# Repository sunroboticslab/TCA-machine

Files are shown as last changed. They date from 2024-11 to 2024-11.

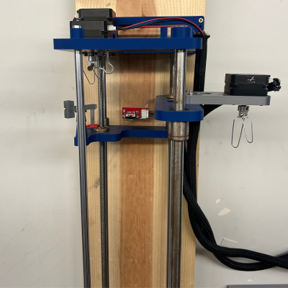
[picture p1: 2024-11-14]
TCA_Machine_Version_2/04 Photos/Picture2.png

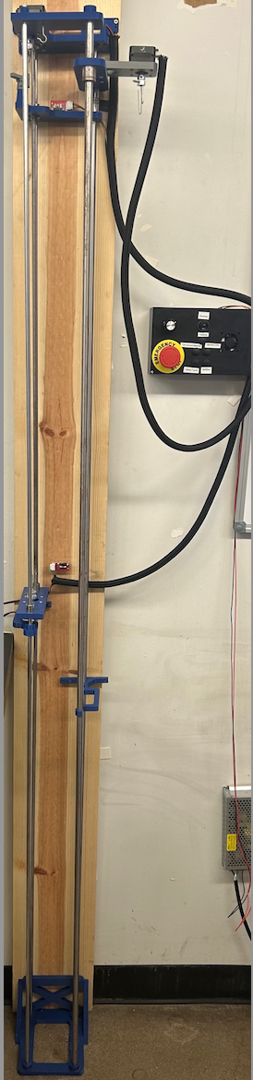
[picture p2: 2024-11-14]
TCA_Machine_Version_2/04 Photos/Picture1.png

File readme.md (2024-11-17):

<h1 align="center">Twisted and Coiled Actuator (TCA) Machine - V1 & V2</h1>

<p>Welcome to the Twisted and Coiled Actuator (TCA) Machine project repository! This project involves the design, manufacturing, and development of two versions of a machine used to fabricate TCAs for soft robotic applications. TCAs mimic biological actuators and are ideal for creating compliant, adaptive, and resilient robots. This repository contains the models, control software, documentation, and more for both versions of the TCA machine.</p>

<h2>Project Overview</h2>

<p>The TCA Machine is an automated fabrication system designed to create free stroke twisted and coiled actuators for use in soft robotic systems. These actuators provide high contraction ratios and are useful for many robotic applications, such as actuating tensegrity robots and shape-morphing quadrupedal robots.</p>

<p>There are two versions of the TCA machine available in this repository:</p>

<ul>
  <li><strong>Version 1</strong></li>
  <li><strong>Version 2</strong></li>
</ul>
<h3>Differences Between Version 1 and Version 2</h3>
<ul>
  <li>Version 2 has an increased width to improve reliability and provide more room for manipulation.</li>
  <li>The pulley in Version 2 is separated from the machine and suspended in the air to reduce friction and tension in the thread.</li>
  <li>A Stepper motor was removed in Version 2 as it was redundant.</li>
  <li>Transition from latch buttons to momentary buttons for improved control.</li>
  <li>Physical limit switches were added in Version 2 for enhanced safety and control.</li>
</ul>

<h2>Repository Structure</h2>

<h3>Version 1: TCA_Machine_Version_1/</h3>
<ul>
  <li><strong>01 SolidWorks</strong>
    <ul>
      <li><strong>01 Machine:</strong> Contains SolidWorks files for the mechanical design of the TCA machine.</li>
      <li><strong>02 Control_Box:</strong> SolidWorks files for the control box design, including details of the electronics.</li>
    </ul>
  </li>
  <li><strong>02 Arduino</strong>: Arduino code to control the motors and sensors of the machine, ensuring precise coiling and twisting.</li>
  <li><strong>03 Documentation</strong>: Contains documentation related to Version 1, which are listed below.
  <ul>
      <li><strong>Parts list TCA machine.xlsx:</strong> An Excel file listing all the parts used in Version 1 of the TCA machine.</li>
      <li><strong>TCA Machine.docx:</strong> Documentation describing the purpose and operation of the TCA machine.</li>
      <li><strong>TCA Manufacturing.pptx:</strong> A PowerPoint presentation that provides insights into the manufacturing process of TCAs.</li>
      <li><strong>motor layout.pptx:</strong> A presentation detailing the layout of the motors used in Version 1.</li>
    </ul>
  </li>
  <li><strong>04 Photos</strong>: A collection of photos showcasing the machine and its components.</li>
</ul>

<h3>Version 2: TCA_Machine_Version_2/</h3>
<ul>
  <li><strong>01 SolidWorks</strong>
    <ul>
      <li><strong>01 Machine</strong>: Updated SolidWorks files for the enhanced mechanical design.</li>
      <li><strong>02 Control_Box</strong>: Updated SolidWorks files for the improved control box design.</li>
    </ul>
  </li>
<li><strong>02 Arduino/TCACodeV2.0</strong>: Improved Arduino code for Version 2, featuring optimizations for smoother operation and enhanced control.</li>
<li><strong>03 Documentation</strong>: Updated user manuals and documentation for assembling and operating Version 2.
    <ul>
    <li><strong>Instructions_manualV2.pdf</strong>: A comprehensive user manual for Version 2, detailing Mechanical Construction, Electrical Construction, and how to use the machine.</li>
    <li><strong>Motor_Layout.pdf</strong>: A PDF document detailing the motor layout in Version 2.</li>
    <li><strong>TCA_Machine_Mech_BOM.xlsx</strong>: Bill of Materials for the mechanical components in Version 2.</li>
    <li><strong>TCA_Machine_Electric_BOM.xlsx</strong>: Bill of Materials for the electrical components in Version 2.</li>
    </ul>
  </li>
  <li><strong>04 Photos</strong>: Photos of Version 2 showcasing the new features and improvements.</li>
</ul>

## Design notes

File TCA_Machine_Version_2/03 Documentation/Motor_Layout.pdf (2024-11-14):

# Motor Layout and Electrical Schematics

# Motor Layout

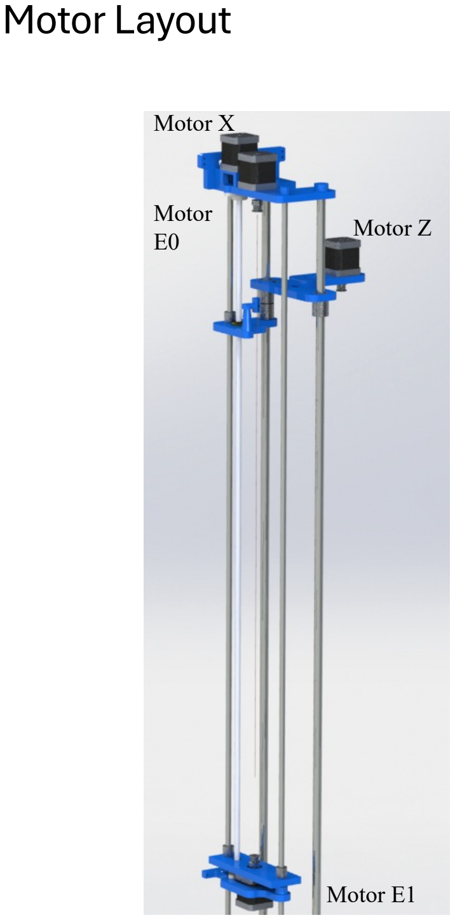
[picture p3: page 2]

Motor X

Motor
E0 | Motor Z

Motor E1

# Electrical Schematics

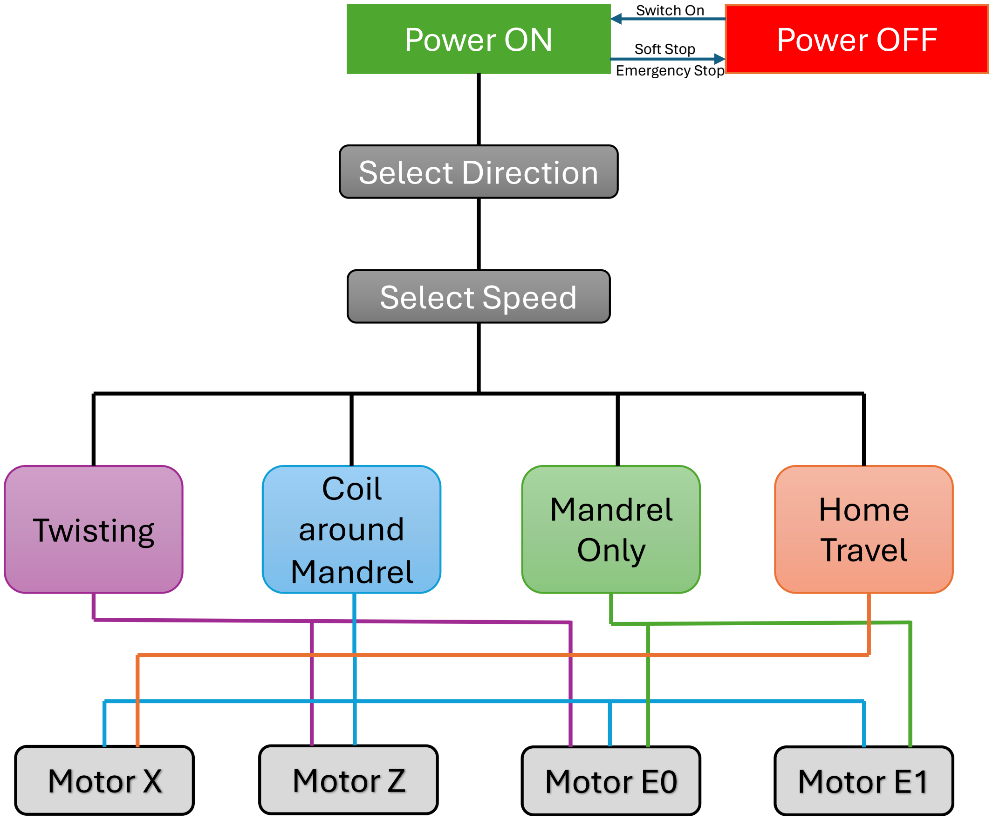
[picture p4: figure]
Power ON; Power OFF; Select Direction; Twisting; Coil around Mandrel; Mandrel Only; Home Travel; Select Speed; Motor X; Motor Z; Motor E0; Motor E1; Soft Stop; Switch On; Emergency Stop

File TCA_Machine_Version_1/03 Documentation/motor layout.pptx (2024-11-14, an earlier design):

## Motor electrical Schematics

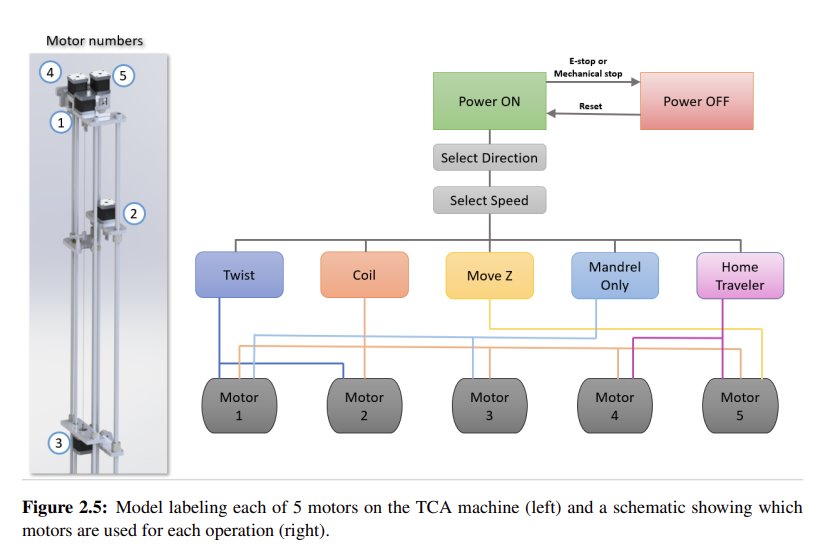
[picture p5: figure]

## Motor Orientation

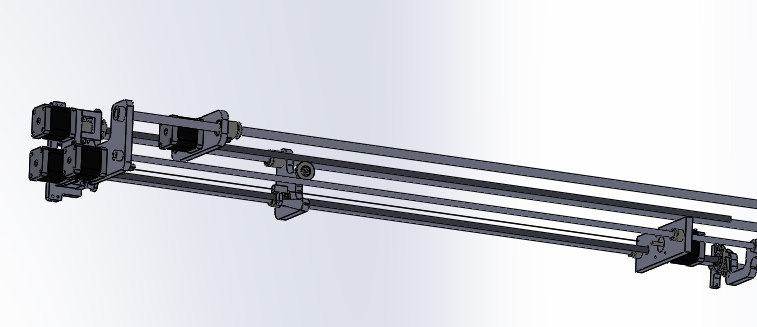
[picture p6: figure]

Y

X

Z

E0

E1

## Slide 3

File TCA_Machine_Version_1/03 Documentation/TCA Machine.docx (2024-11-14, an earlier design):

The customized machine for fabrication of the Twisted-and-Coiled Actuators.

The machine’s high is 1.8 m and we can install a precursor fiber around 3.2 m by folding the fiber around a roller at the bottom of the machine. That will allow the machine to fabricate a TCA with maximum length of 1 m within 8 min for a proficient user. The machine can be used to fabricate either extension TCA or contraction TCAs.

A control panel is installed and there are functioning buttons that can control fabrication speed, reset the machine, control individual motors and motor directions. The machine has 5 step motor that control the twisting and coiling process. Motor A and B insert twisting into a precursor fiber from the two ends of the fiber. Motor C and D rotate the mandrel and motor E control the traveling to coil the twisted fiber on a mandrel.

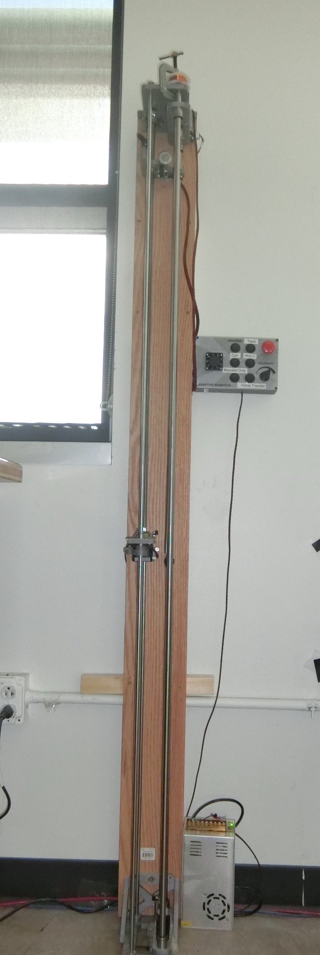
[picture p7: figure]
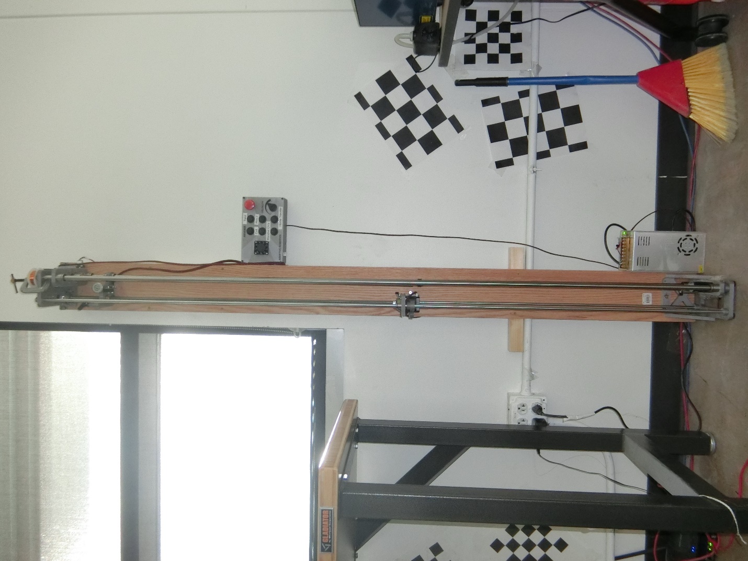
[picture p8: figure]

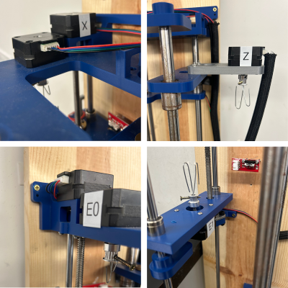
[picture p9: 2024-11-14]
TCA_Machine_Version_2/04 Photos/Picture4.png

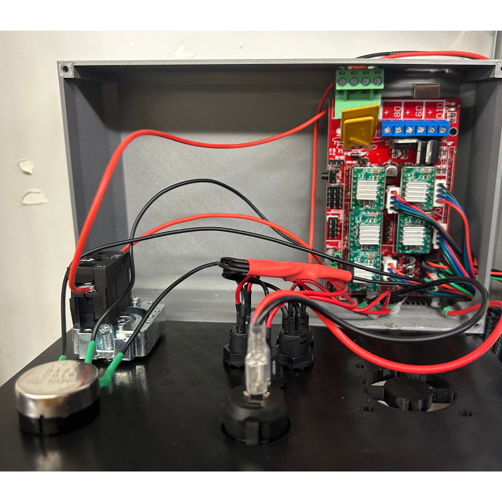
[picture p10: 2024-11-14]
TCA_Machine_Version_2/04 Photos/Picture3.png

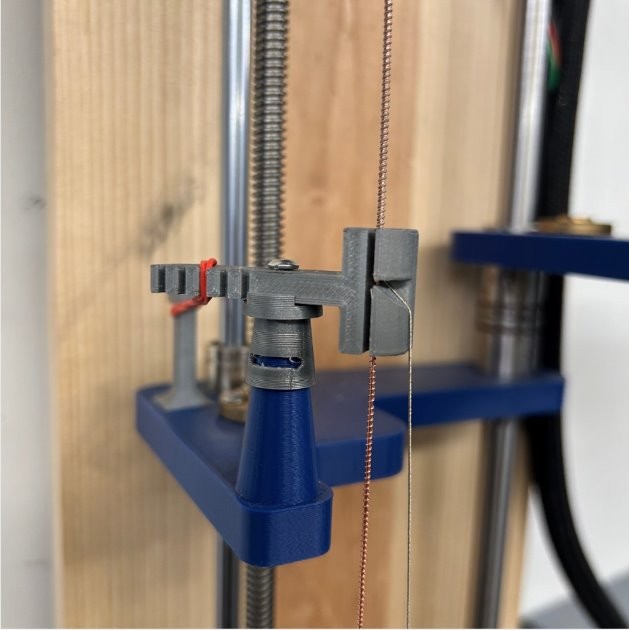
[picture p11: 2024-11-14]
TCA_Machine_Version_2/04 Photos/Picture5.jpg

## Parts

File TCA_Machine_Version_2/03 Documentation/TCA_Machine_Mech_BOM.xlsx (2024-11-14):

Name | Quantity | Unit Price | Total Price | Link
Mechanical Parts
2 meters guide rod (12mm dia) | 2 | 78.42 | 156.84 | https://www.mcmaster.com/6112K55/
1 meter guide rod (8mm) | 4 | 33.99 | 135.96 | https://a.co/d/fRVqcEy
T8 Lead Screw Set (Pitch 2mm, Lead 2mm, Length 1000mm) | 1 | 29.75 | 29.75 | https://a.co/d/94WhODm
12mm LM12UU Linear Motion Ball Bearing (10 set) | 1 | 17.21 | 17.21 | https://a.co/d/ehVNYda
8mm LM8UU Linear Motion Ball Bearing(10 Set) | 1 | 9.99 | 9.99 | https://a.co/d/6VYYZox
KFL08 Pillow Block Bearing 8mm/0.31"(4 Set) | 1 | 8.99 | 8.99 | https://a.co/d/cz1D3lo
Wood (1 in. x 12 in. x 12 ft.) | 1 | 37.98 | 37.98 | https://www.homedepot.com/p/1-in-x-12-in-x-12-ft-Premium-Kiln-Dried-Square-Edge-Whitewood-Common-Softwood-Boards-458554/100088520
Screw Hooks (.080 x 1-5/16') | 1 | 2.59 | 2.59 | https://a.co/d/eZcLpH0
M3 Button Head Screws | 1 | 16.99 | 16.99 | https://a.co/d/c4Ccx2F
M5 Button Head Screws | 1 | 7.29 | 7.29 | https://a.co/d/cdViFu4
GT2 Timing Belt Pulleys (5 Set) | 1 | 7.99 | 7.99 | https://a.co/d/6UJ3atT
Total |  |  | 431.58

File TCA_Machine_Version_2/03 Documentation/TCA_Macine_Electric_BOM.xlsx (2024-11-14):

Name | Quantity | Unit Price | Total Price | Link
Electrical Parts
NEMA 17 motors (5 Set) | 1 | 38.99 | 38.99 | https://a.co/d/bTNgY0k
NEMA 17 motor control kit (RAMPS 1.4 Controller + Arduino Mega 2560 + A4988 Motor Drivers) | 1 | 31.23 | 31.23 | https://a.co/d/d4WsQai
Mechanical EndStop Limit Switches | 1 | 8.99 | 8.99 | https://a.co/d/cJqhPcu
12mm Mini Momentary Push Button Switches(12 Set) | 1 | 9.96 | 9.96 | https://a.co/d/cWaeGQx
Emergency Stop Push Button Switch | 1 | 9.99 | 9.99 | https://a.co/d/iSiMs7G
Potentiometer | 1 | 9.55 | 9.55 | https://a.co/d/dMHleoA
12V 10A DC Universal Regulated Switching Power Supply | 1 | 24.41 | 24.41 | https://a.co/d/bmSqOKI
26 Gauge Bare Copper Wire | 1 | 7.99 | 7.99 | https://a.co/d/bAmWfGY
30 Gauge Bare Copper Wire | 1 | 9.99 | 9.99 | https://a.co/d/aIDjfT3
22 Gauge Silicone Wires | 1 | 12.48 | 12.48 | https://a.co/d/0CMNqas
12V Round Rocker Switch | 1 | 4.99 | 4.99 | https://a.co/d/810Gv5C
Power Chord | 1 | 9.99 | 9.99 | https://a.co/d/27jVXjj
Total |  |  | 178.56

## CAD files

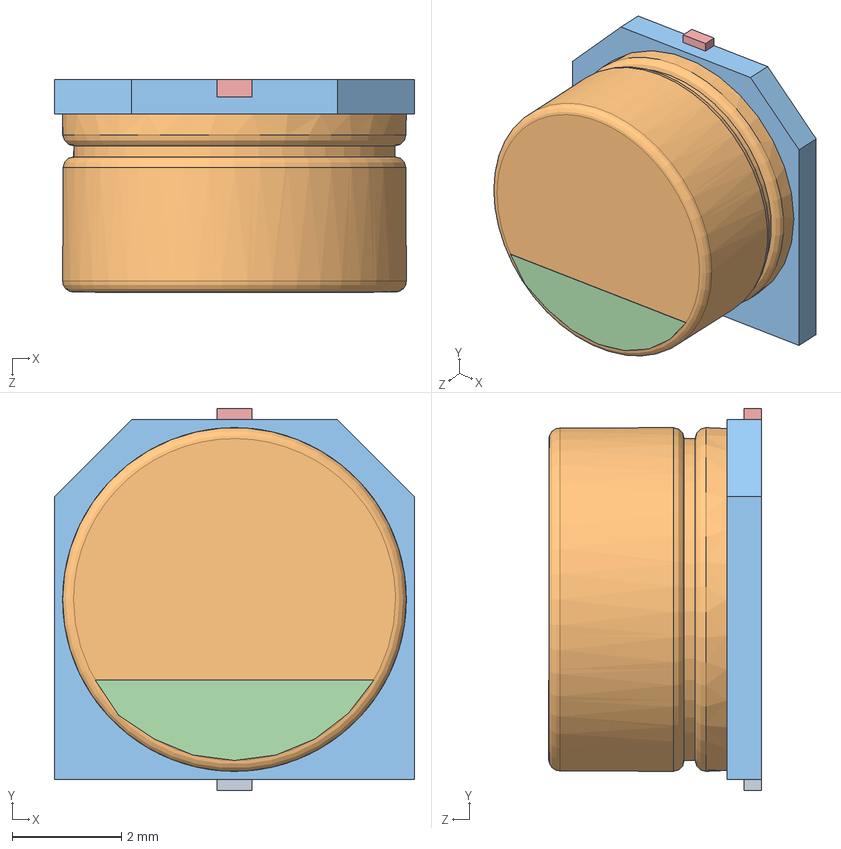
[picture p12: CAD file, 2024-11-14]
TCA_Machine_Version_2/01 SolidWorks/02 Control_Box/V2_User Library-CAPSMD6_3x3_9.SLDASM
6.60 x 7.00 x 3.91 mm
User Library-CAPSMD6_3x3_9_CAP003
User Library-CAPSMD6_3x3_9_CAP
User Library-CAPSMD6_3x3_9_CAP001
User Library-CAPSMD6_3x3_9_CAP002
User Library-CAPSMD6_3x3_9_CAP004

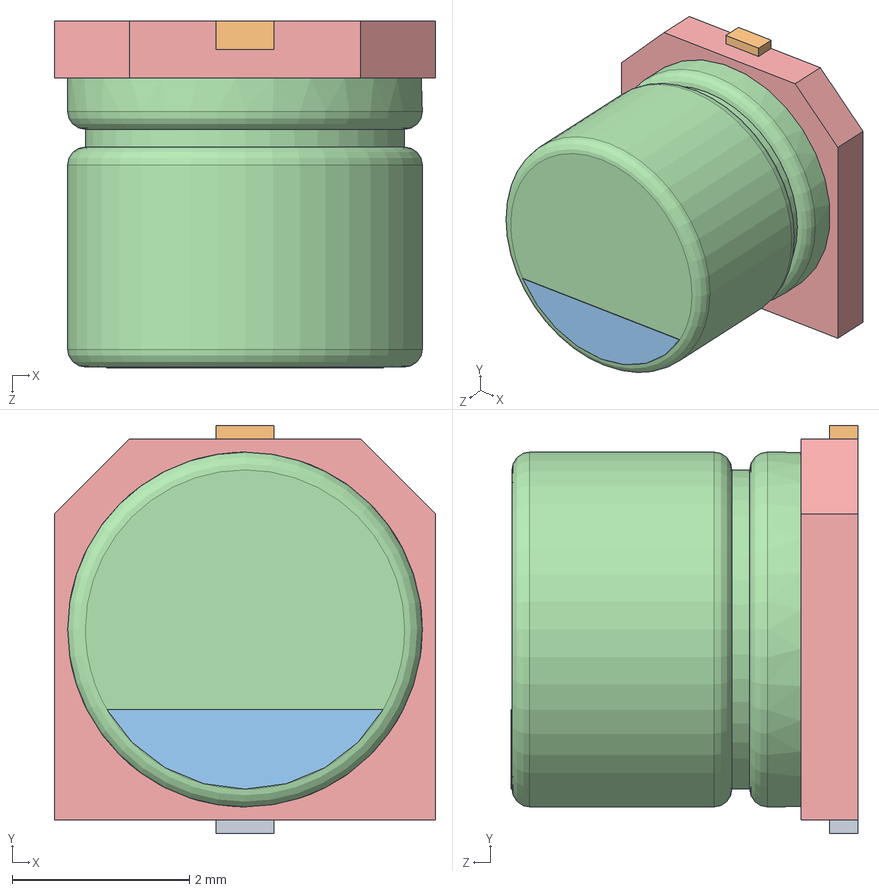
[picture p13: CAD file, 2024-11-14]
TCA_Machine_Version_2/01 SolidWorks/02 Control_Box/V2_User Library-CAPSMD4x3_9.SLDASM
4.30 x 4.60 x 3.91 mm
User Library-CAPSMD4x3_9_CAPSMD4x3_9003
User Library-CAPSMD4x3_9_CAPSMD4x3_9004
User Library-CAPSMD4x3_9_CAPSMD4x3_9002
User Library-CAPSMD4x3_9_CAPSMD4x3_9001
User Library-CAPSMD4x3_9_CAPSMD4x3_9

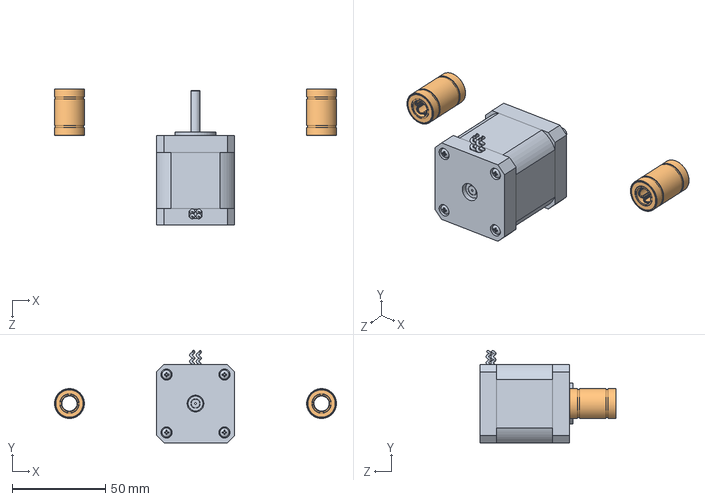
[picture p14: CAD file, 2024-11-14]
TCA_Machine_Version_2/01 SolidWorks/01 Machine/V2_TSA machine motor on sliderV2.SLDASM
151.0 x 49.5 x 73.0 mm
V2_8mm LINEAR BALL BEARNGV2 x 2
V2_Stepper Motor NEMA 17 42x42x50V2

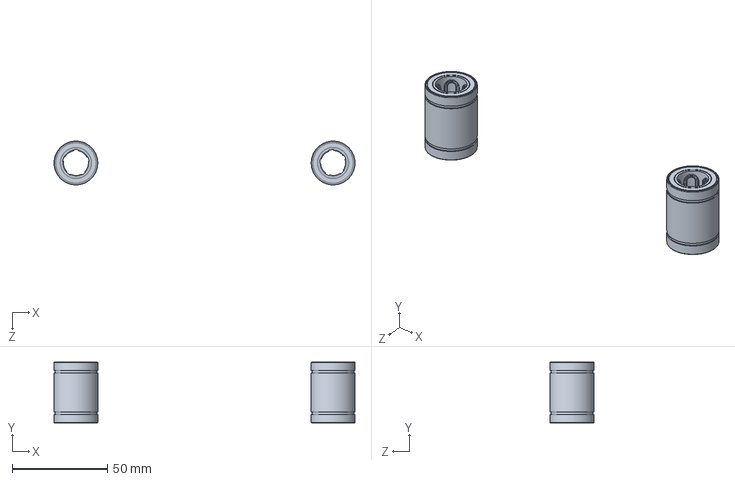
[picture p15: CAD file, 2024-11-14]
TCA_Machine_Version_2/01 SolidWorks/01 Machine/V2_TSA machine motor on slider 13mmV2.SLDASM
158.0 x 32.0 x 23.0 mm
V2_13mm LINEAR BALL BEARNGV2 x 2

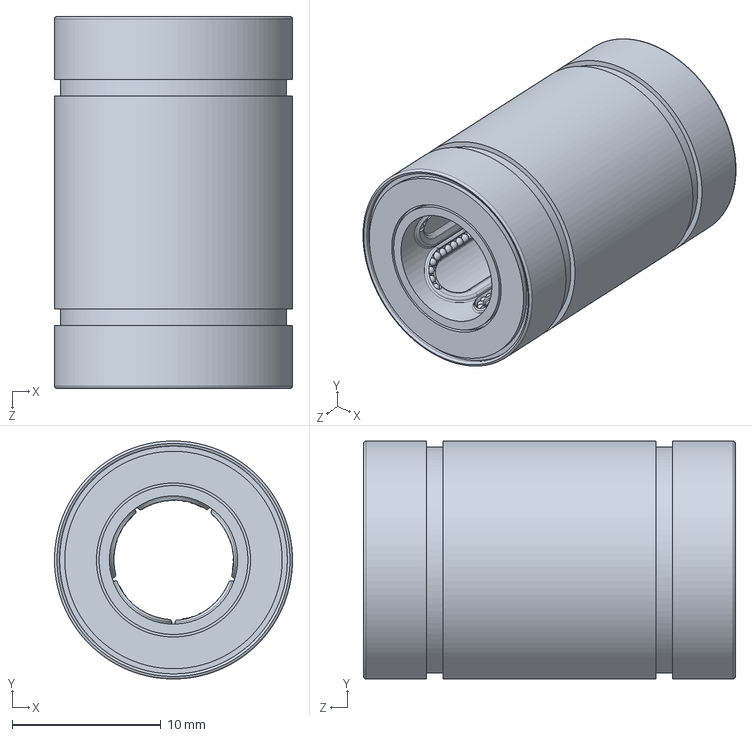
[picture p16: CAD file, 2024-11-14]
TCA_Machine_Version_2/01 SolidWorks/01 Machine/V2_8mm LINEAR BALL BEARNGV2.SLDPRT
16.0 x 16.0 x 25.0 mm

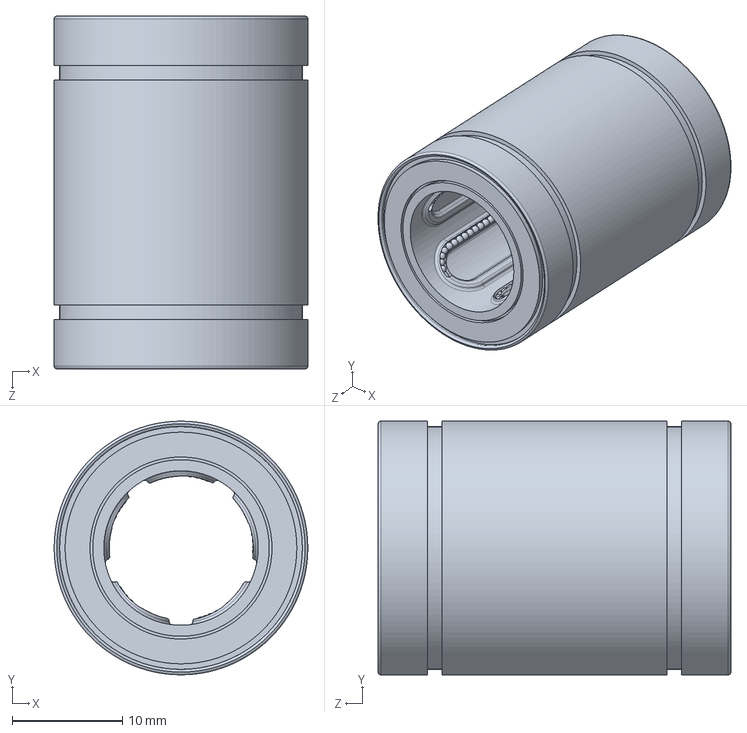
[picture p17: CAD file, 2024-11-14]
TCA_Machine_Version_2/01 SolidWorks/01 Machine/V2_13mm LINEAR BALL BEARNGV2.SLDPRT
23.0 x 23.0 x 32.0 mm

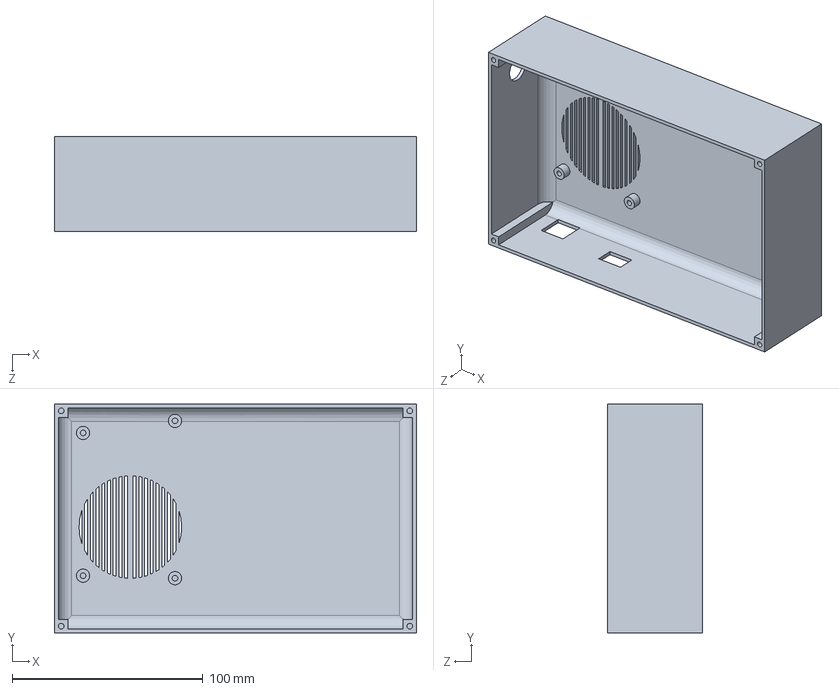
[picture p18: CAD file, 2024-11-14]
TCA_Machine_Version_2/01 SolidWorks/02 Control_Box/V2_control case bottom_latest10-2-2024.SLDPRT
190.0 x 120.0 x 50.0 mm

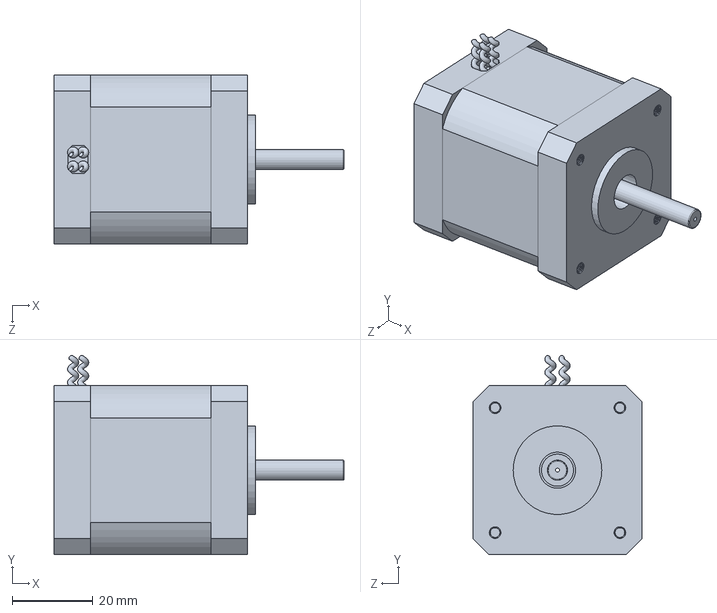
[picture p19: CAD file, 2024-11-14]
TCA_Machine_Version_2/01 SolidWorks/01 Machine/V2_Stepper Motor NEMA 17 42x42x50V2.SLDPRT
72.0 x 49.5 x 42.0 mm

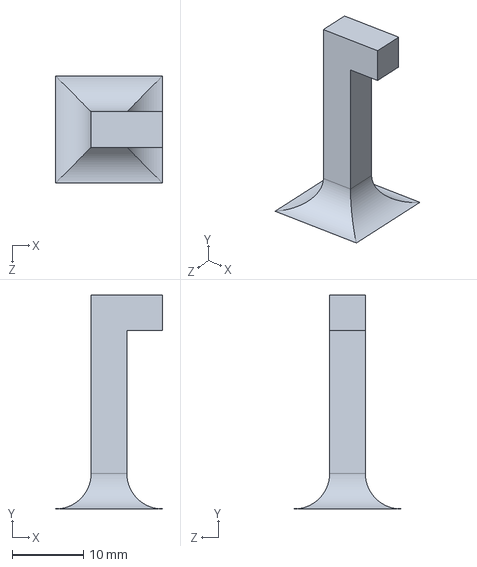
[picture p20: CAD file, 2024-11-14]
TCA_Machine_Version_2/01 SolidWorks/01 Machine/V2_demoextraV2.SLDPRT
15.0 x 30.0 x 15.0 mm

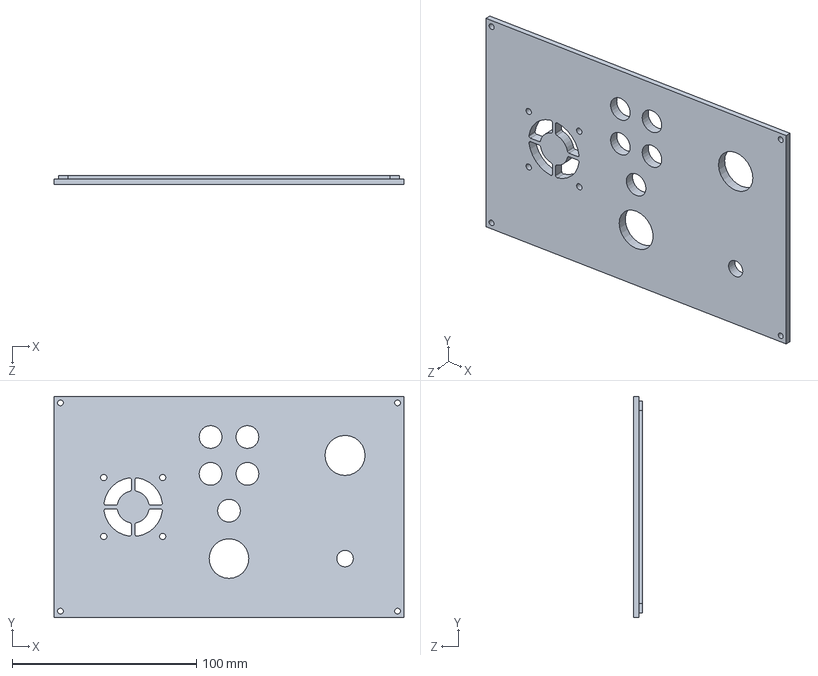
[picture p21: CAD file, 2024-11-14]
TCA_Machine_Version_2/01 SolidWorks/02 Control_Box/V2_control case top_latest10-2-2024.SLDPRT
190.0 x 120.0 x 5.00 mm

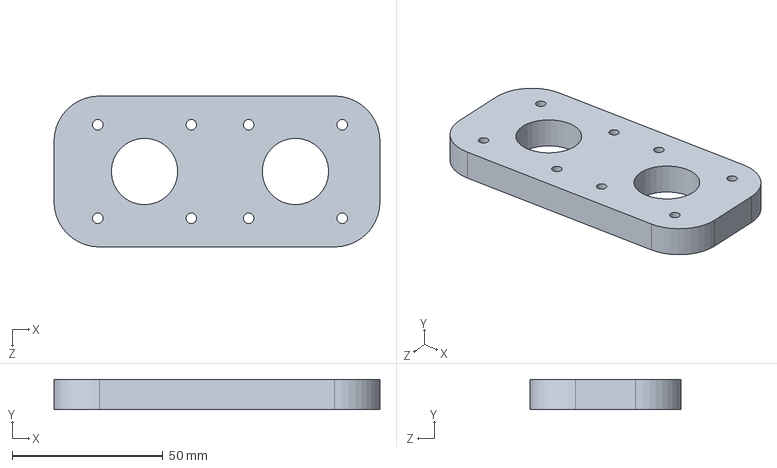
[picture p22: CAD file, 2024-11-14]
TCA_Machine_Version_2/01 SolidWorks/01 Machine/V2_TSA machine 1m plateextensionV2.SLDPRT
108.0 x 10.0 x 50.0 mm

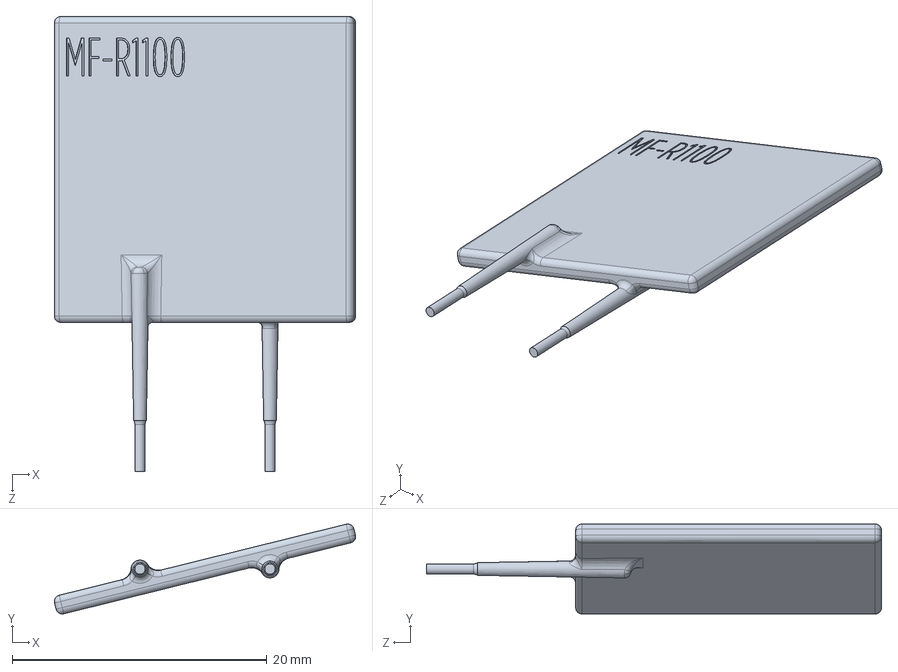
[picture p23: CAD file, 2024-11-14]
TCA_Machine_Version_2/01 SolidWorks/02 Control_Box/V2_User Library-MF-R1100.SLDPRT
23.6 x 7.06 x 35.7 mm

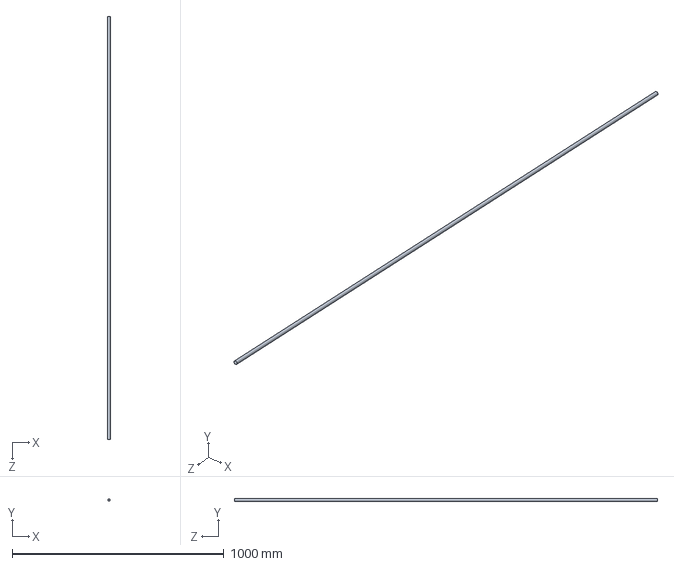
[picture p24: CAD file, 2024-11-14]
TCA_Machine_Version_2/01 SolidWorks/01 Machine/V2_steel (threaded) ROD 12mm x 2000mmV2.SLDPRT
12.0 x 12.0 x 2000.0 mm

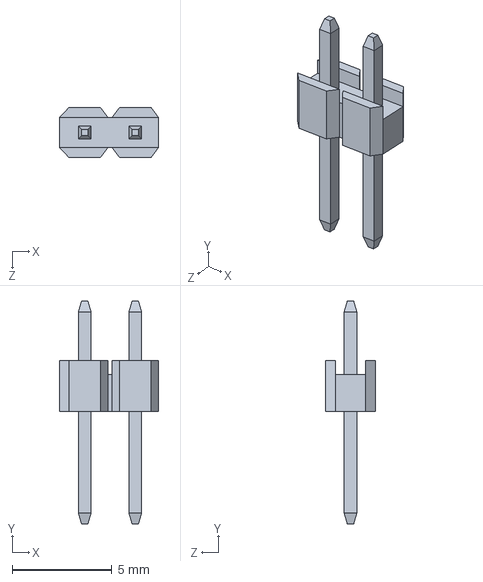
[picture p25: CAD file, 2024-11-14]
TCA_Machine_Version_2/01 SolidWorks/02 Control_Box/V2_pin_header_aw140-eg-g02d.SLDPRT
4.98 x 11.2 x 2.50 mm

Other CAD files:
TCA_Machine_Version_2/01 SolidWorks/02 Control_Box/01 V2_TCA conrol.SLDASM
TCA_Machine_Version_2/01 SolidWorks/01 Machine/V2_5395T213_ 8mm SHAFT COUPLINGV2.SLDPRT
TCA_Machine_Version_2/01 SolidWorks/02 Control_Box/V2_User Library-MF-R500.SLDPRT
TCA_Machine_Version_2/01 SolidWorks/01 Machine/V2_TSA machine 1m connector plateV2.SLDPRT
TCA_Machine_Version_1/01 SolidWorks/01 Machine/V113mm LINEAR BALL BEARNG.SLDPRT
TCA_Machine_Version_1/01 SolidWorks/01 Machine/V1250 g brass mass.SLDPRT
TCA_Machine_Version_1/01 SolidWorks/01 Machine/V13434T220_PULLEY FOR WIRE ROPE 1.0625in OD.SLDPRT
TCA_Machine_Version_1/01 SolidWorks/01 Machine/V15395T213_ 8mm SHAFT COUPLING.SLDPRT
TCA_Machine_Version_1/01 SolidWorks/01 Machine/V15912K780_ 8mm MOUNTED SLEEVE BEARING.SLDPRT
TCA_Machine_Version_1/01 SolidWorks/01 Machine/V18mm LINEAR BALL BEARNG.SLDPRT
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

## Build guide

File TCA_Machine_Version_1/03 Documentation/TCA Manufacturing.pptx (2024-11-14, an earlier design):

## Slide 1

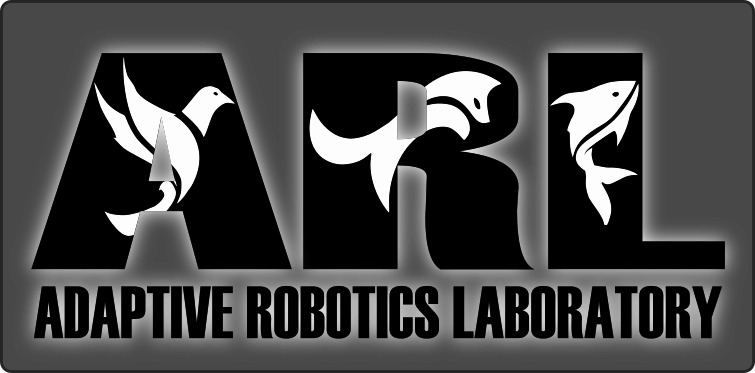
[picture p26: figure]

## TCA Manufacturing

Adaptive Robotics Laboratory

## Twisted Coil Actuator

Materials:
- Conductive Nylon thread
  - PN#200121235364HCB
  - 235/36 dtex 4 ply HCB
  - V Technical Textiles, Inc.
- 26 ga copper wire (core)
- 32 ga copper wire (guide channel)
Useful information:
- Anneal 2 hours at 185° C
- Use “Step Calculator” in Parts List TCA Machine excel sheet to adjust lengths
- For “Type i” TCA
  - Natural thread length for full size TCA is 3.6 m
  - Twist 2160 times (216,000 steps/ motor)

## STEPS

1. Cut 26 ga wire (core) to desired length and twist loops in each end.
2. Connect to top and bottom mandrel motors (locate on the left side).
3. Twist loop in 32 ga (guide) wire, attach to the same side hook as the core wire and unwind approximately 3x the length of the 26 core wire.
4. Run 32 ga guide wire through lower pulley and tighten spool on top of machine (ensure proper mass is on lower pulley mounting plate).
5. At MEDIUM speed, use MANDREL ONLY function to secure guide wire to core and position it to insert into the follower guide.
6. With guide wire in guide and tensioner rubber bands on, at the SECOND TO HIGHEST speed, press COIL button and closely monitor the traveler, manually stop at bottom of the TCA.
7. Use MANDREL ONLY function to secure guide wire to core, then cut and tie off guide wire.
8. Remove mandrel from top motor and place on side hook.
9. Home travelers using HOME TRAVELERS button.

10. Cut thread to length (depending on helical angle / desired TCA length) and tie loops on each end.
11. Connect to left and right top motor hooks, running through lower pulley (ensure proper mass is on lower pulley mounting plate).
12. On HIGH speed, press TWIST button (remember to turn off button when operation is complete!)
13. Replace top of mandrel to the top motor on the opposite side hook as twisted thread.
14. Repeat steps 6-8 to coil and secure both ends of twisted thread to mandrel.
15. Remove TCA from lower hook and twist a loop in the end to “lock” thread. Repeat with top.
16. Home travelers using HOME TRAVELERS button.
17. Anneal in the oven for 2 hours at 185° C.
18. Untwist loops and cut guide wire and begin to manually unwind it at the top of the TCA.
19. Attach to mandrel motors and while holding the unwound end of the guide wire, at MEDIUM speed push MANDREL ONLY button to unwind guide wire.
20. Remove from machine, cut ends and pull mandrel core out of TCA.

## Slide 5

Updated code for the TCA machine can be found here:
https://github.com/bztighe/Arduino-Code/tree/master/TCA%20Machine
Additional resources including Excel book with parts list, wiring diagrams, length/ step calculator, etc:
https://drive.google.com/drive/folders/1GMNalh82XPEKqc4Yx6E1d4W8H_9g_3dO
More information about Dr. Jianguo Zhao and the Adaptive Robotic Laboratory can be found here:
https://www.engr.colostate.edu/~zhao/

All of the content of this video is property of Dr. Jianguo Zhao and the Adaptive Robotics Laboratory at Colorado State University. Unauthorized use, replication, or distribution of this video or any of the content therein without direct and written consent from its owner is strictly prohibited.

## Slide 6

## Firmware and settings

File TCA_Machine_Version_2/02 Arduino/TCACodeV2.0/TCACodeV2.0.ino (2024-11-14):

#include <AccelStepper.h> // Including the AccelStepper library to control stepper motors

// Motor pin configurations for step, direction, and enable
#define X_STEP_PIN    54  
#define X_DIR_PIN     55  
#define X_ENABLE_PIN  38  

#define Y_STEP_PIN    60  
#define Y_DIR_PIN     61  
#define Y_ENABLE_PIN  56  

#define Z_STEP_PIN    46  
#define Z_DIR_PIN     48  
#define Z_ENABLE_PIN  62  

#define E0_STEP_PIN   26  
#define E0_DIR_PIN    28  
#define E0_ENABLE_PIN 24  

#define E1_STEP_PIN   36  
#define E1_DIR_PIN    34  
#define E1_ENABLE_PIN 30  

// Pin configurations for mechanical stops and control buttons
#define X_MIN_PIN     3   // Limit switch for X axis minimum position
#define Y_MIN_PIN     14  // Limit switch for Y axis minimum position

#define BUTTON_PIN1   40  // Buttons for mode selection
#define BUTTON_PIN2   42  
#define BUTTON_PIN3   44  
#define BUTTON_PIN4   39  
#define BUTTON_PIN5   47  
#define REVERSE_BUTTON_PIN 16  // Button to reverse direction
#define RESET_BUTTON_PIN 23    // Button to reset the system

// Analog pin configuration for speed control
int SpeedPot = A9;
#define out 27 // Unused output pin

// Creating stepper motor objects using the AccelStepper library
AccelStepper stepperX(AccelStepper::DRIVER, X_STEP_PIN, X_DIR_PIN);  
AccelStepper stepperY(AccelStepper::DRIVER, Y_STEP_PIN, Y_DIR_PIN); 
AccelStepper stepperZ(AccelStepper::DRIVER, Z_STEP_PIN, Z_DIR_PIN); 
AccelStepper stepperE0(AccelStepper::DRIVER, E0_STEP_PIN, E0_DIR_PIN); 
AccelStepper stepperE1(AccelStepper::DRIVER, E1_STEP_PIN, E1_DIR_PIN); 

// State and control variables
bool softStop = false;    // Flag for soft stop control
bool reverse = false;     // Flag to indicate direction reversal
int potValue = 0;         // Potentiometer value for speed control
int CoilSpeed;            // Speed of coiling motor
int buttonMode = 0;       // Mode selected by button input
const int stepsPerRevolution = 400;  // Steps per motor revolution
bool X_MIN = 0;           // State of X axis minimum limit switch
bool X_MAX = 0;           // State of X axis maximum limit switch
int xmin = 0;             // Placeholder for X axis minimum state

// Speed settings and movement ratios
float speedRatio = .4857;           // Ratio for speed control
float untwistRatio = 0.2;         // Untwist ratio to compensate twisting during coiling
const int MaxSpeed = 1000;        // Maximum speed for all motors

// Motor movement distance settings
long TravelerSteps = 160000;      // Steps for traveler lead screw movement
long MandralSteps = 1333333;      // Steps for mandrel coiling motor movement
long twisting = 432000;           // Steps for twisting motor movement

void setup() {
  // Initialize serial communication for debugging
  Serial.begin(9600);

  // Configure pins for mechanical stops and control buttons
  pinMode(X_MIN_PIN, INPUT_PULLUP);  
  pinMode(Y_MIN_PIN, INPUT_PULLUP);  
  pinMode(BUTTON_PIN1, INPUT_PULLUP); 
  pinMode(BUTTON_PIN2, INPUT_PULLUP); 
  pinMode(BUTTON_PIN3, INPUT_PULLUP); 
  pinMode(BUTTON_PIN4, INPUT_PULLUP); 
  pinMode(BUTTON_PIN5, INPUT_PULLUP); 
  pinMode(REVERSE_BUTTON_PIN, INPUT_PULLUP);
  pinMode(RESET_BUTTON_PIN, INPUT_PULLUP);   

  // Configure pins for enabling stepper motors
  pinMode(X_ENABLE_PIN, OUTPUT);  
  pinMode(Y_ENABLE_PIN, OUTPUT);  
  pinMode(Z_ENABLE_PIN, OUTPUT);  
  pinMode(E0_ENABLE_PIN, OUTPUT); 
  pinMode(E1_ENABLE_PIN, OUTPUT); 

  // Set the maximum speed for each stepper motor
  stepperX.setMaxSpeed(MaxSpeed);
  stepperY.setMaxSpeed(MaxSpeed);
  stepperZ.setMaxSpeed(MaxSpeed);
  stepperE0.setMaxSpeed(MaxSpeed);
  stepperE1.setMaxSpeed(MaxSpeed);
}
void loop() {
  // Read button inputs to determine the current mode of operation
  if (digitalRead(BUTTON_PIN1) == LOW) {
    buttonMode = 1;  // Mode 1: Twisting operation
  } else if (digitalRead(BUTTON_PIN2) == LOW) {
    buttonMode = 2;  // Mode 2: Coil around mandrel with traveler
  } else if (digitalRead(BUTTON_PIN3) == LOW) {
    buttonMode = 3;  // Mode 3: Coil copper around mandrel
  } else if (digitalRead(BUTTON_PIN4) == LOW) {
    buttonMode = 4;  // Mode 4: Move traveler lead screw only
  } else if (digitalRead(BUTTON_PIN5) == LOW) {
    buttonMode = 5;  // Mode 5: Reset and home all motors
  } else {
    buttonMode = 0;  // No button pressed, reset all steppers
    resetAllSteppers();
  }

  // Set motor speed based on potentiometer input
  potValue = analogRead(SpeedPot);
  int range = map(potValue, 0, 1023, 0, 5);

  // Map potentiometer value to coil speed
  switch (range) {
    case 0: 
      CoilSpeed = 140;
      break;
    case 1:  
      CoilSpeed = 330;
      break;
    case 2:   
      CoilSpeed = 520;
      break;
    case 3:
      CoilSpeed = 685; 
      break;
    case 4:   
      CoilSpeed = 800; 
      break;
    case 5:   
      CoilSpeed = 1000; 
      break;
  }

  // Calculate the speed for the traveler motor based on the coil speed
  float TravelSpeed = CoilSpeed * speedRatio;

  // Mode 1: Twisting thread
  if (buttonMode == 1) {
    reverse = digitalRead(REVERSE_BUTTON_PIN) == LOW;  // Check if reverse button is pressed
    long position = reverse ? -twisting : twisting;    // Set direction based on reverse flag
    digitalWrite(Z_ENABLE_PIN, LOW);                   // Enable Z motor
    digitalWrite(E0_ENABLE_PIN, LOW);                  // Enable E0 motor

    // Set positions and speeds for motors
    stepperZ.moveTo(position);
    stepperE0.moveTo(-position);
    stepperZ.setSpeed(CoilSpeed);
    stepperE0.setSpeed(CoilSpeed);

    // Run motors to positions until the required distance is reached or conditions to stop are met
    long distance = position;
    while (abs(distance) > 10) {
      if (digitalRead(BUTTON_PIN5) == LOW) { resetAllSteppers(); break; }  // Stop if button 5 is pressed
      if (digitalRead(X_MIN_PIN) == LOW) { resetAllSteppersX(); break; }   // Stop if X limit switch is triggered
      if (digitalRead(Y_MIN_PIN) == LOW) { resetAllSteppersY(); break; }   // Stop if Y limit switch is triggered
      stepperZ.runSpeedToPosition();
      stepperE0.runSpeedToPosition();
      distance = stepperE0.distanceToGo();
    }
  }

  // Mode 2: Coil around mandrel with traveler movement
  if (buttonMode == 2) {
    reverse = digitalRead(REVERSE_BUTTON_PIN) == LOW;  // Check if reverse button is pressed
    long position1 = reverse ? MandralSteps : -MandralSteps;
    long position2 = reverse ? -TravelerSteps : TravelerSteps;

    // Enable all motors
    digitalWrite(X_ENABLE_PIN, LOW);
    digitalWrite(Y_ENABLE_PIN, LOW);
    digitalWrite(Z_ENABLE_PIN, LOW);
    digitalWrite(E0_ENABLE_PIN, LOW);
    digitalWrite(E1_ENABLE_PIN, LOW);

    // Set positions and speeds for motors
    stepperX.moveTo(position2);
    stepperY.moveTo(position2);
    stepperZ.moveTo(position1);
    stepperE0.moveTo(position1);
    stepperE1.moveTo(position1);
    stepperX.setSpeed(TravelSpeed);
    stepperY.setSpeed(TravelSpeed);
    stepperZ.setSpeed(CoilSpeed * untwistRatio);
    stepperE0.setSpeed(CoilSpeed);
    stepperE1.setSpeed(CoilSpeed);

    // Run motors to positions until the required distance is reached or conditions to stop are met
    long distance = position2;
    while (abs(distance) > 10) {
      if (digitalRead(BUTTON_PIN5) == LOW) { resetAllSteppers(); break; }  // Stop if button 5 is pressed
      if (digitalRead(X_MIN_PIN) == LOW) { resetAllSteppersX(); break; }   // Stop if X limit switch is triggered
      if (digitalRead(Y_MIN_PIN) == LOW) { resetAllSteppersY(); break; }   // Stop if Y limit switch is triggered
      stepperX.runSpeedToPosition();
      stepperY.runSpeedToPosition();
      stepperZ.runSpeedToPosition();
      stepperE0.runSpeedToPosition();
      stepperE1.runSpeedToPosition();
      distance = stepperX.distanceToGo();
    }
  }

  // Mode 3: Coil copper around mandrel (no traveler movement)
  if (buttonMode == 3) {
    reverse = digitalRead(REVERSE_BUTTON_PIN) == LOW;  // Check if reverse button is pressed
    long position = reverse ? MandralSteps : -MandralSteps;

    // Enable E0 and E1 motors
    digitalWrite(E0_ENABLE_PIN, LOW);
    digitalWrite(E1_ENABLE_PIN, LOW);

    // Set positions and speeds for motors
    stepperE0.moveTo(position);
    stepperE1.moveTo(position);
    stepperE0.setSpeed(CoilSpeed);
    stepperE1.setSpeed(CoilSpeed);

    // Run motors to positions until the required distance is reached or conditions to stop are met
    long distance = abs(position);
    while (abs(distance) > 10) {
      if (digitalRead(BUTTON_PIN5) == LOW) { resetAllSteppers(); break; }
      if (digitalRead(X_MIN_PIN) == LOW) { resetAllSteppersX(); break; }
      if (digitalRead(Y_MIN_PIN) == LOW) { resetAllSteppersY(); break; }
      stepperE0.runSpeedToPosition();
      stepperE1.runSpeedToPosition();
      distance = stepperE0.distanceToGo();
    }
  }

  // Mode 4: Move traveler lead screw only
  if (buttonMode == 4) {
    reverse = digitalRead(REVERSE_BUTTON_PIN) == LOW;  // Check if reverse button is pressed
    long position = reverse ? TravelerSteps : -TravelerSteps;

    // Enable X and Y motors
    digitalWrite(X_ENABLE_PIN, LOW);
    digitalWrite(Y_ENABLE_PIN, LOW);

    // Set positions and speeds for motors
    stepperX.moveTo(position);
    stepperY.moveTo(position);
    stepperX.setSpeed(CoilSpeed);
    stepperY.setSpeed(CoilSpeed);

    // Run motors to positions until the required distance is reached or conditions to stop are met
    long distance = position;
    while (abs(distance) > 10) {
      if (digitalRead(BUTTON_PIN5) == LOW) { resetAllSteppers(); break; }
      if (digitalRead(X_MIN_PIN) == LOW) { resetAllSteppersX(); break; }
      if (digitalRead(Y_MIN_PIN) == LOW) { resetAllSteppersY(); break; }
      stepperX.runSpeedToPosition();
      stepperY.runSpeedToPosition();
      distance = stepperX.distanceToGo();
    }
  }

  // Mode 5: Reset all motors and stop
  if (buttonMode == 5) {
    resetAllSteppers();
    delay(10);
  }

  // No button pressed
  if (buttonMode == 0) {
    delay(10);
  }

  softStop = false;  // Reset soft stop flag
}

// Function to reset all stepper motors and set positions to zero
void resetAllSteppers() {
  // Stop all stepper motors and reset positions to zero
  stepperX.stop();
  stepperY.stop();
  stepperZ.stop();
  stepperE0.stop();
  stepperE1.stop();
  stepperX.setCurrentPosition(0);
  stepperY.setCurrentPosition(0);
  stepperZ.setCurrentPosition(0);
  stepperE0.setCurrentPosition(0);
  stepperE1.setCurrentPosition(0);

  // Disable all stepper motor drivers
  digitalWrite(X_ENABLE_PIN, HIGH); 
  digitalWrite(Y_ENABLE_PIN, HIGH);
  digitalWrite(Z_ENABLE_PIN, HIGH);
  digitalWrite(E0_ENABLE_PIN, HIGH);
  digitalWrite(E1_ENABLE_PIN, HIGH);

  softStop = false;  // Reset the soft stop flag
}

void resetAllSteppersX() {
  // Stop all stepper motors and reset positions to zero
  stepperX.stop();
  stepperY.stop();
  stepperZ.stop();
  stepperE0.stop();
  stepperE1.stop();
  stepperX.setCurrentPosition(0);
  stepperY.setCurrentPosition(0);
  stepperZ.setCurrentPosition(0);
  stepperE0.setCurrentPosition(0);
  stepperE1.setCurrentPosition(0);

  // Disable all stepper motor drivers
  digitalWrite(X_ENABLE_PIN, HIGH); 
  digitalWrite(Y_ENABLE_PIN, HIGH);
  digitalWrite(Z_ENABLE_PIN, HIGH);
  digitalWrite(E0_ENABLE_PIN, HIGH);
  digitalWrite(E1_ENABLE_PIN, HIGH);

  // Move X motor to position 500 and reset position
  digitalWrite(X_ENABLE_PIN, LOW);  // Enable X motor
  stepperX.moveTo(500);
  stepperX.setSpeed(1000);

  long distance = 500;
  while (abs(distance) > 10) {
    stepperX.runSpeedToPosition();
    distance = stepperX.distanceToGo();
  }

  stepperX.stop();
  stepperX.setCurrentPosition(0);  // Reset position after movement

  digitalWrite(X_ENABLE_PIN, HIGH); // Disable X motor after movement

  softStop = false;  // Reset the soft stop flag

  // Stop all stepper motors again and reset positions
  stepperX.stop();
  stepperY.stop();
  stepperZ.stop();
  stepperE0.stop();
  stepperE1.stop();
  stepperX.setCurrentPosition(0);
  stepperY.setCurrentPosition(0);
  stepperZ.setCurrentPosition(0);
  stepperE0.setCurrentPosition(0);
  stepperE1.setCurrentPosition(0);

  // Disable all stepper motor drivers
  digitalWrite(X_ENABLE_PIN, HIGH); 
  digitalWrite(Y_ENABLE_PIN, HIGH);
  digitalWrite(Z_ENABLE_PIN, HIGH);
  digitalWrite(E0_ENABLE_PIN, HIGH);
  digitalWrite(E1_ENABLE_PIN, HIGH);

  softStop = false;  // Reset the soft stop flag
}

void resetAllSteppersY() {
  // Stop all stepper motors and reset positions to zero
  stepperX.stop();
  stepperY.stop();
  stepperZ.stop();
  stepperE0.stop();
  stepperE1.stop();
  stepperX.setCurrentPosition(0);
  stepperY.setCurrentPosition(0);
  stepperZ.setCurrentPosition(0);
  stepperE0.setCurrentPosition(0);
  stepperE1.setCurrentPosition(0);

  // Disable all stepper motor drivers
  digitalWrite(X_ENABLE_PIN, HIGH); 
  digitalWrite(Y_ENABLE_PIN, HIGH);
  digitalWrite(Z_ENABLE_PIN, HIGH);
  digitalWrite(E0_ENABLE_PIN, HIGH);
  digitalWrite(E1_ENABLE_PIN, HIGH);

  // Move X motor to position -500 and reset position
  digitalWrite(X_ENABLE_PIN, LOW);  // Enable X motor
  stepperX.moveTo(-500);
  stepperX.setSpeed(1000);

  long distance = -500;
  while (abs(distance) > 10) {
    stepperX.runSpeedToPosition();
    distance = stepperX.distanceToGo();
  }

  stepperX.stop();
  stepperX.setCurrentPosition(0);  // Reset position after movement

  digitalWrite(X_ENABLE_PIN, HIGH); // Disable X motor after movement

  softStop = false;  // Reset the soft stop flag

  // Stop all stepper motors again and reset positions
  stepperX.stop();
  stepperY.stop();
  stepperZ.stop();
  stepperE0.stop();
  stepperE1.stop();
  stepperX.setCurrentPosition(0);
  stepperY.setCurrentPosition(0);
  stepperZ.setCurrentPosition(0);
  stepperE0.setCurrentPosition(0);
  stepperE1.setCurrentPosition(0);

  // Disable all stepper motor drivers
  digitalWrite(X_ENABLE_PIN, HIGH); 
  digitalWrite(Y_ENABLE_PIN, HIGH);
  digitalWrite(Z_ENABLE_PIN, HIGH);
  digitalWrite(E0_ENABLE_PIN, HIGH);
  digitalWrite(E1_ENABLE_PIN, HIGH);

  softStop = false;  // Reset the soft stop flag
}
